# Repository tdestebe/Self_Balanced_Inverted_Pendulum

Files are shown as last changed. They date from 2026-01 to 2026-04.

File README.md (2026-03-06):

# Self_Balanced_Inverted_Pendulum

Self Balanced Inverted Pendulum

This project aims to build an inverted pendulum stabilized by a single reaction wheel. The position of the pendulum is detected by a 3-axis analog gyroscope sensor (MPU6050 module). The position is analyzed inside an Arduino Nano that sends appropriate signals to a motor (Nidec 24H404H160). 

## 3D CAD Model

The assembly of the CAD models and parts are designed with FreeCAD. Following worbenchs are used:

- **Part design** to design 3D mechanical parts

- **Assembly 4.1** based on local axis systems

- **Fasteners** for all screws and nuts

- **Mesh** to create and export STL files

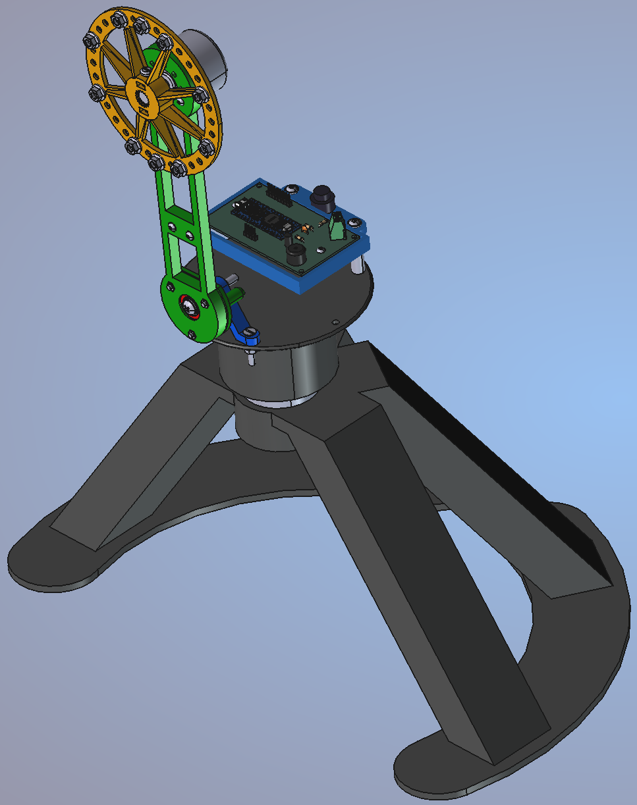
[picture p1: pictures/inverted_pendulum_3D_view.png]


**Inverted pendulum - FreeCAD mesh export**

FreeCAD files are available at [freeCad](https://github.com/tdestebe/Self_Balanced_Inverted_Pendulum/tree/main/freeCad)

STL 3D files are at [STL_files](https://github.com/tdestebe/Self_Balanced_Inverted_Pendulum/tree/main/STL_files)

## Simulation with openModelica

Simulation is performed through an openModelica implementation into the package SelfBalancedWheelPackage. Main Modelica model **SingleWheelRobot** calls model **Dynamics** in which PID, Motor, etc are implemented and calls model **Animation** to display rotation of 3D models of the reaction wheel and the arm. 

thumbnail

**Inverted pendulum - Modelica main model**

<table border="0" style="width: 100%;">
  <!-- Current Row -->
  <tr>
    <th style="border: none; text-align: center; font-weight: bold;">thumbnail</th>
    <th style="border: none; text-align: center; font-weight: bold;"></th>
    <th style="border: none; text-align: center; font-weight: bold;">thumbnail</th>
  </tr>
  <!-- Header Rows -->
  <tr>
    <td style="border: none;"><b>Inverted pendulum - Modelica Dynamics model</b></td>
    <td style="border: none; text-align: center; font-weight: bold;"></td>
    <td style="border: none;"><b>Inverted pendulum - Modelica Animation model</b></td>
  </tr>
</table>

Source files are available at [Self Balaced Wheel Package](https://github.com/tdestebe/Self_Balanced_Inverted_Pendulum/tree/main/SelfBalancedWheelPackage)

## Arduino code and circuits

### Code (.ino)

The source code for Arduino is provided at [code](https://github.com/tdestebe/Self_Balanced_Inverted_Pendulum/tree/main/code). It is similar to the code written by **Remigijus** (see [remrc - One-Axis-Reaction-Wheel-Stick](https://github.com/remrc/One-Axis-Reaction-Wheel-Stick)).

### Fritzing schema

The schema is also identical to the original one posted by Remigijus. I just rewrote it with Fritzing, including a breadboard and stored the source at [circuit](https://github.com/tdestebe/Self_Balanced_Inverted_Pendulum/tree/main/circuit).

<table border="0" style="width: 100%;">
  <!-- Current Row -->
  <tr>
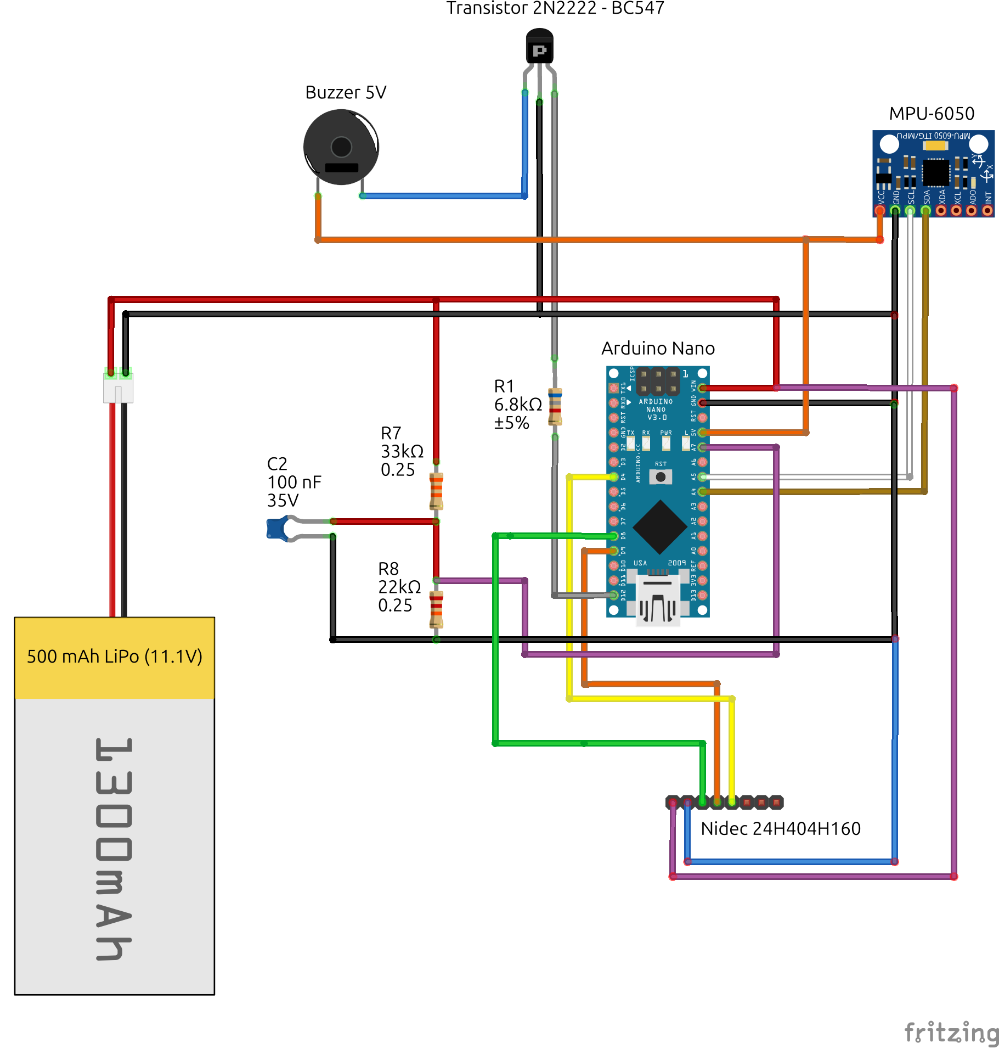
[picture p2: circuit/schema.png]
    <th style="border: none; text-align: center; font-weight: bold;"></th>
    <th style="border: none; text-align: center; font-weight: bold;"></th>
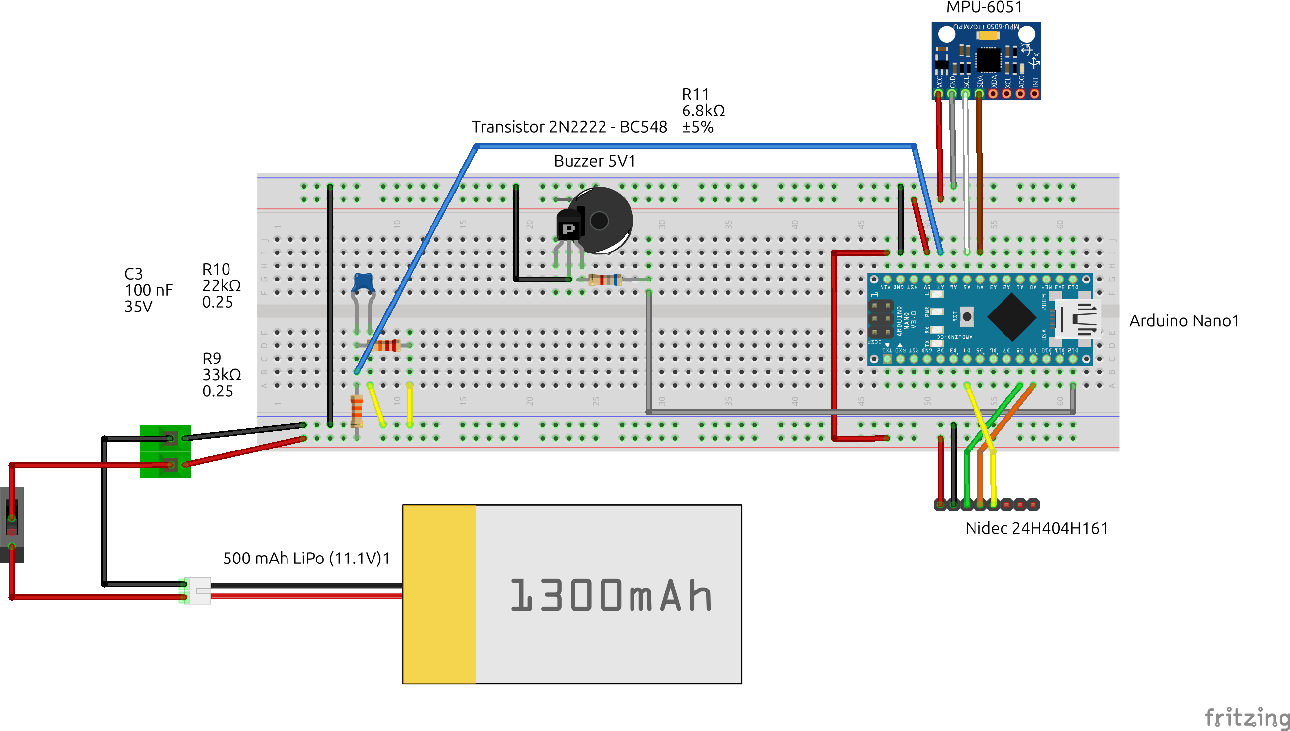
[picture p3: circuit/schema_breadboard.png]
    <th style="border: none; text-align: center; font-weight: bold;"></th>
  </tr>
  <!-- Header Rows -->
  <tr>
    <td style="border: none;"><b>Fritzing schema - Original</b></td>
    <td style="border: none; text-align: center; font-weight: bold;"></td>
    <td style="border: none;"><b>Fritzing schema - Breadboard</b></td>
  </tr>
</table>

### KiCad circuit

In addition to Fritzing schema, I implemented KiCad schematic circuit and generated a KiCad PCB for visualisation into the 3D CAD assembly. 

Kicad project is stored at [kiCAD](https://github.com/tdestebe/Self_Balanced_Inverted_Pendulum/tree/main/kiCAD).

<table border="0" style="width: 100%;">
  <!-- Current Row -->
  <tr>
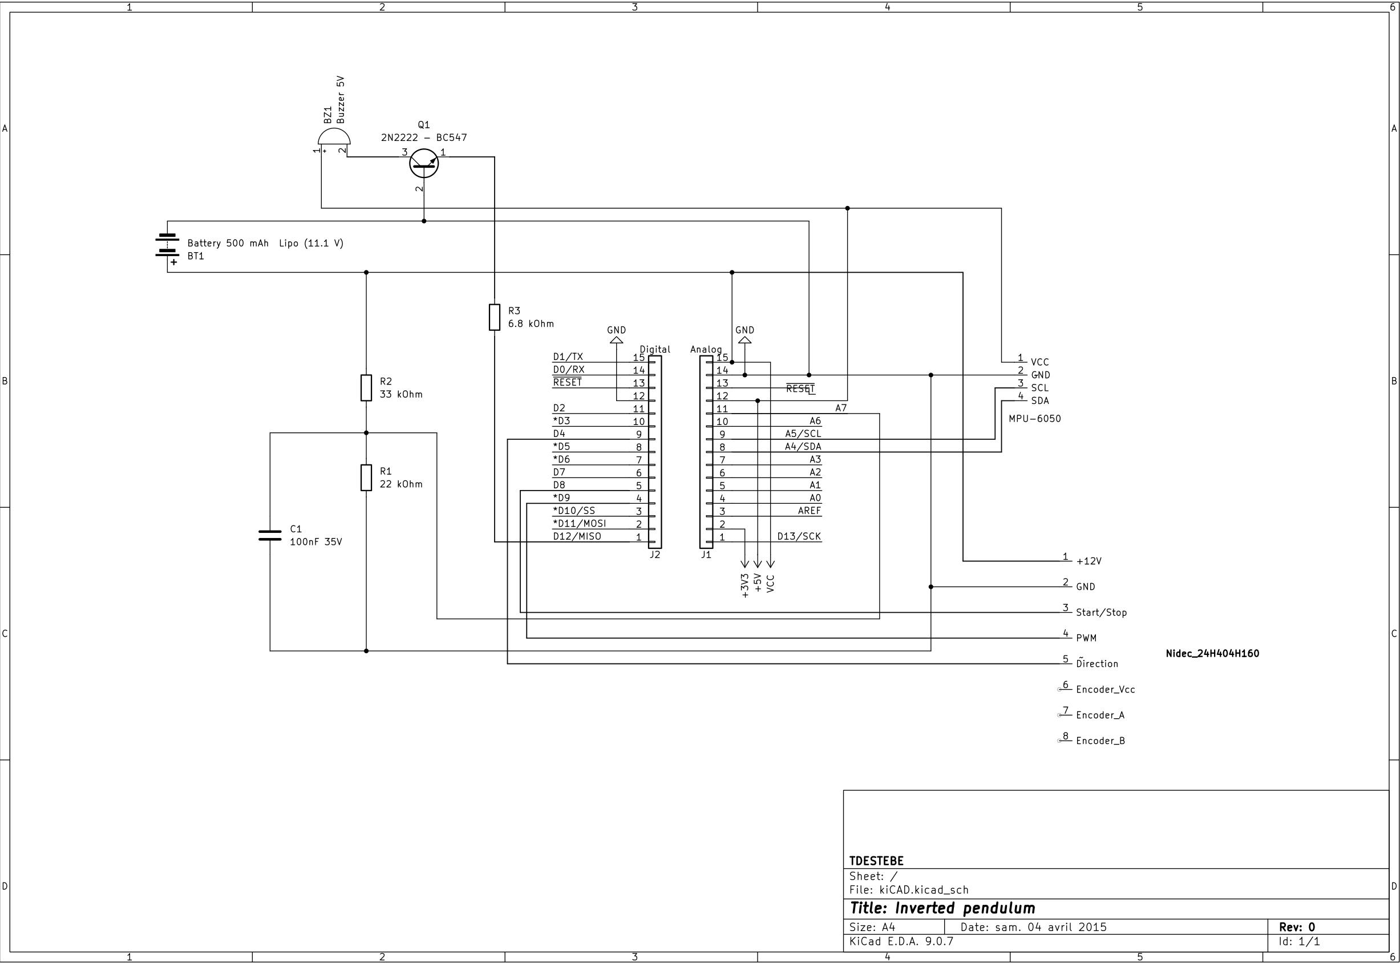
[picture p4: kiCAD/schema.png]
    <th style="border: none; text-align: center; font-weight: bold;"></th>
    <th style="border: none; text-align: center; font-weight: bold;"></th>
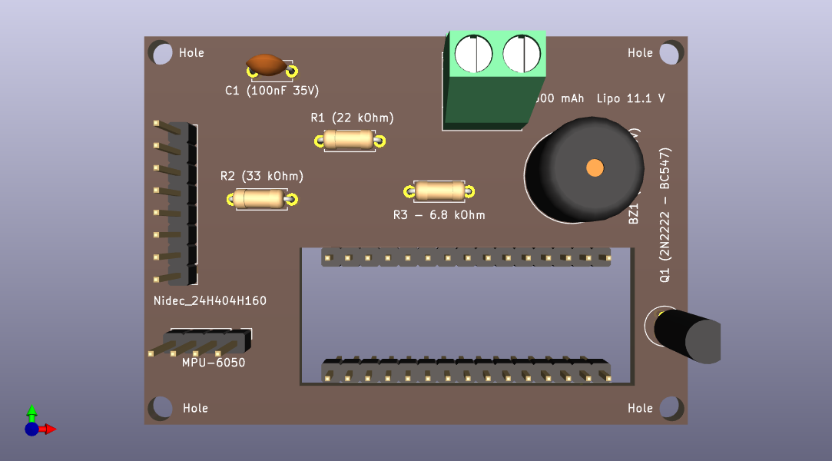
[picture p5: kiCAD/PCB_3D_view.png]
    <th style="border: none; text-align: center; font-weight: bold;"></th>
  </tr>
  <!-- Header Rows -->
  <tr>
    <td style="border: none;"><b>KiCad circuit - Schema</b></td>
    <td style="border: none; text-align: center; font-weight: bold;"></td>
    <td style="border: none;"><b>KiCad circuit - PCD 3D view</b></td>
  </tr>
</table>

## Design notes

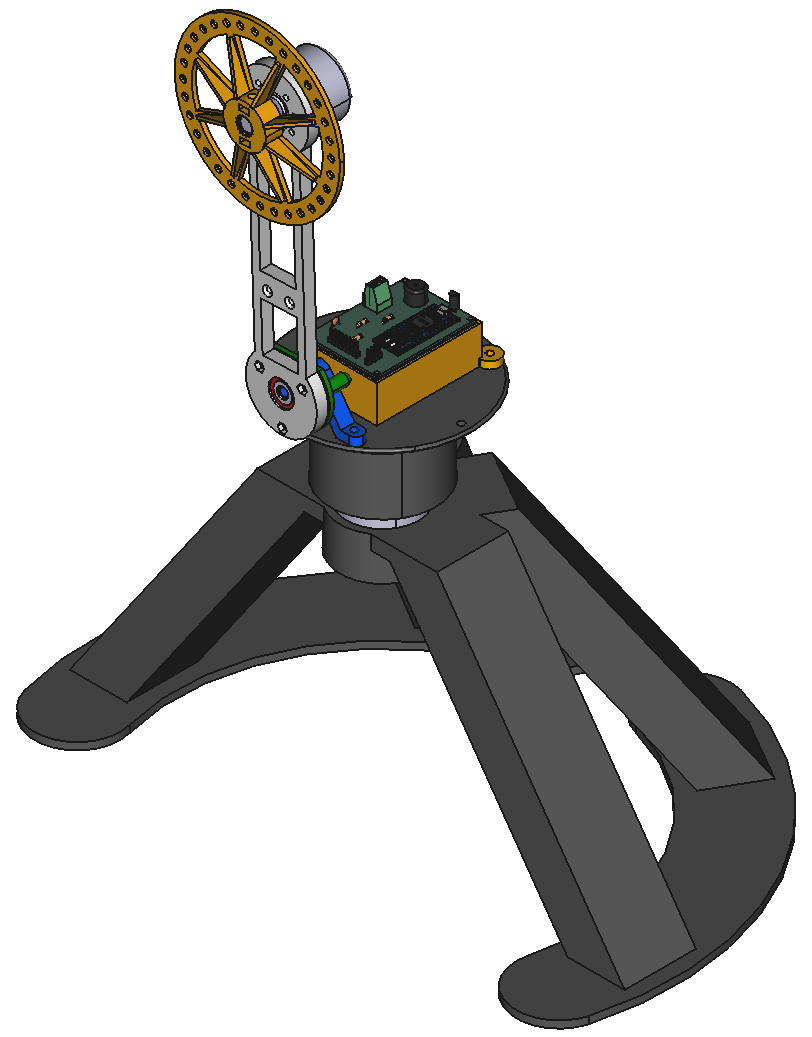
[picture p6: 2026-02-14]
SelfBalancedWheelPackage/robot.png

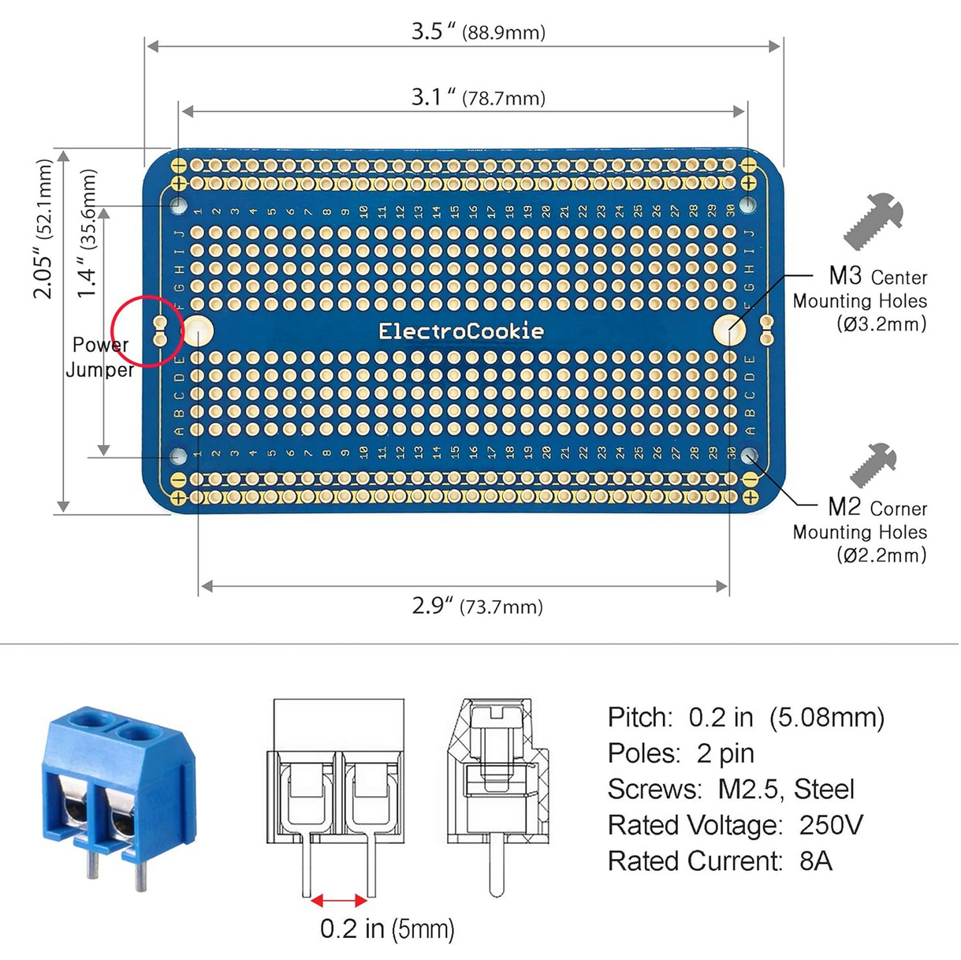
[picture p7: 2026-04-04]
freeCad/ProtoBoard/PCB_prototypage.png

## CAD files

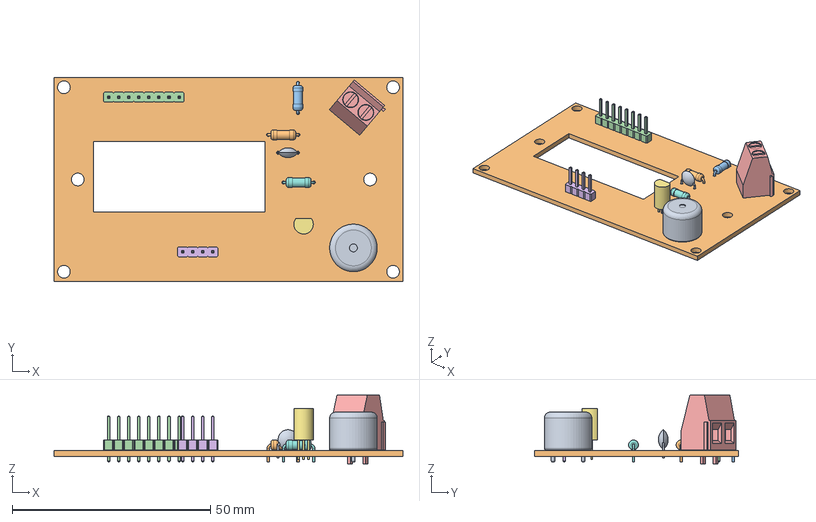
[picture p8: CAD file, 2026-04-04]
freeCad/main_circuit_board.FCStd
88.0 x 51.5 x 17.3 mm
C_Disc_D5.0mm_W2.5mm_P5.00mm
R_Axial_DIN0207_L6.3mm_D2.5mm_P7.62mm_Horizontal
R_Axial_DIN0207_L6.3mm_D2.5mm_P7.62mm_Horizontal001
PinHeader_1x08_P2.54mm_Vertical
TerminalBlock_Phoenix_MKDS-1,5-2_1x02_P5.00mm_Horizontal
PinHeader_1x04_P2.54mm_Vertical
TO-92L_Inline
R_Axial_DIN0207_L6.3mm_D2.5mm_P7.62mm_Horizontal002
Buzzer_12x9.5RM7.6
kiCAD_PCB

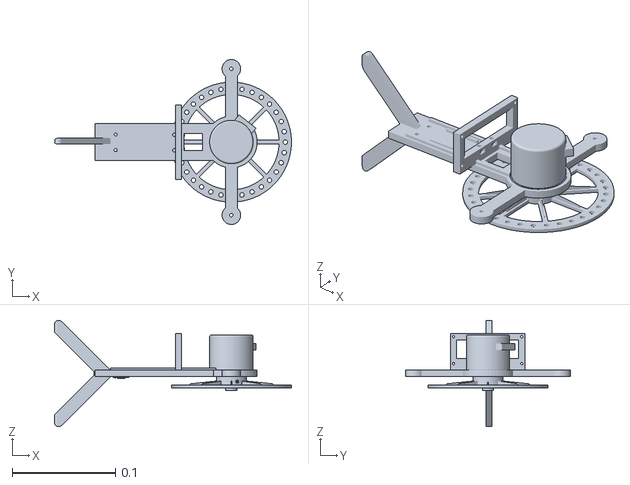
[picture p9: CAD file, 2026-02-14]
SelfBalancedWheelPackage/Resources/assembly_all_meshed.stl
0.229 x 0.159 x 0.103

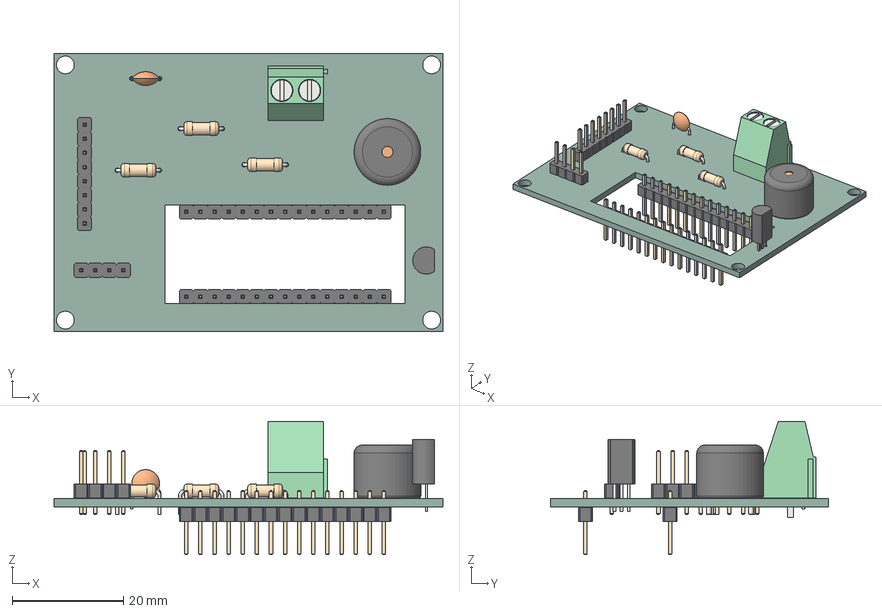
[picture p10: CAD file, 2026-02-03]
freeCad/main_Circuit-kicad_Circuit.STEP
70.0 x 50.0 x 24.0 mm
C_Disc_D5.0mm_W2.5mm_P5.00mm
R_Axial_DIN0207_L6.3mm_D2.5mm_P7.62mm_Horizontal x 3
PinHeader_1x08_P2.54mm_Vertical
TerminalBlock_Phoenix_MKDS-1,5-2_1x02_P5.00mm_Horizontal
PinHeader_1x04_P2.54mm_Vertical
TO-92L_Inline
Buzzer_12x9.5RM7.6
PinHeader_1x15_P2.54mm_Vertical x 2
kicadTest_PCB

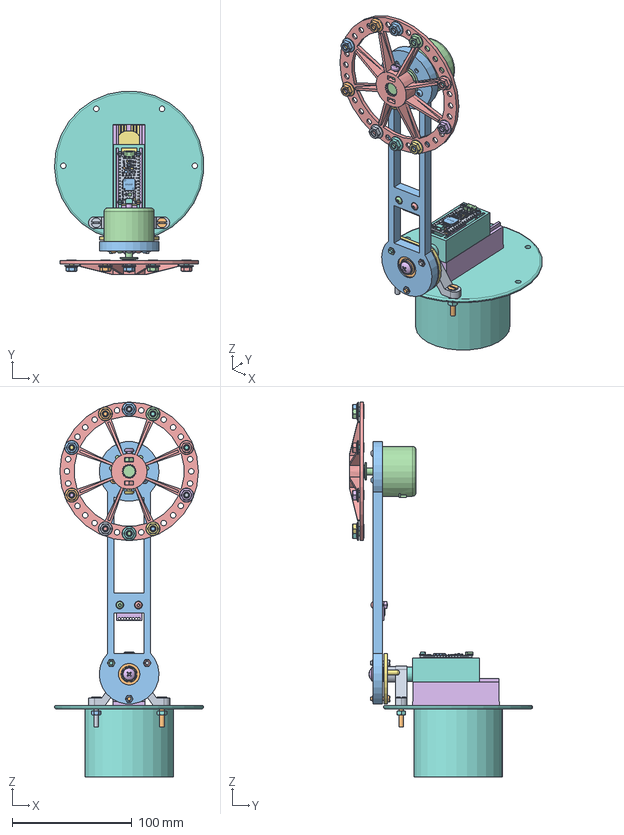
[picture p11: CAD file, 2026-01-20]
freeCad/assembly_Pendulum.FCStd
124.7 x 153.5 x 313.7 mm
Body_Support
Body_Bearing
Body_Arm
Body_Motor
Body_ReactionWheel
Body_MPU6050
Body_BearingLock
Body_Box_Arduino
CAP-0402
FER-0603
CAP-0603
Extruded
SOT-23
lead
lead001
RES-0402
Leader
Leader001
Leader002
Extruded001
Extruded002
RES-0403
RES-0404
RES-0405
Extruded003
Extruded004
Extruded005
Extruded006
CAP-0604
sot25
CAP-0605
RES-0406
RES-0407
RES-0408
RES-0409
SOT-024
SM04B-SRSS-TB_RGB12040119
quartz_3_2__2_5_16MHz v2
RES-0410
RES-0411
RES-0412
RES-0413
FER-0604
CAP-0606
CAP-0607
CAP-0608
CAP-0609
CAP-0610
CAP-0611
CAP-0612
CAP-0613
CAP-0614
Leader003
Leader004
Leader005
Leader006
Leader007
Leader008
Leader009
Leader010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

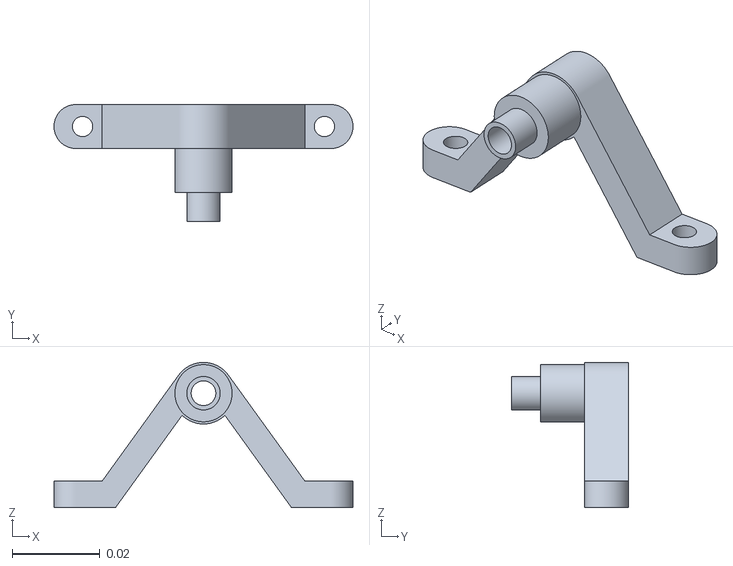
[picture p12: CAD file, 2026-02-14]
SelfBalancedWheelPackage/Resources/Shapes/scale_Simu-04_Support.stl
0.068 x 0.0266 x 0.033

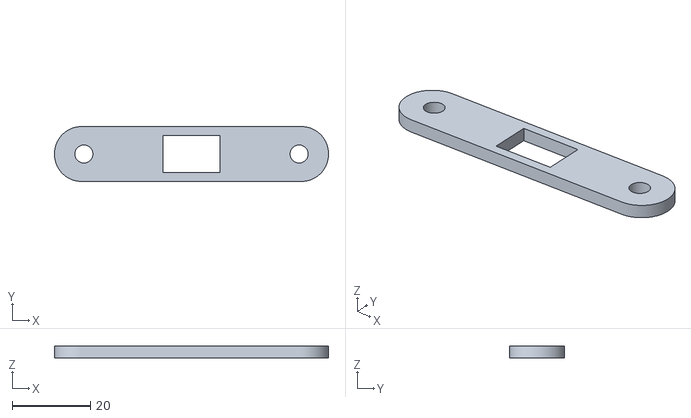
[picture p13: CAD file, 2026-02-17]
STL_files/Body_button_handle (Meshed).stl
70.0 x 14.0 x 3.00

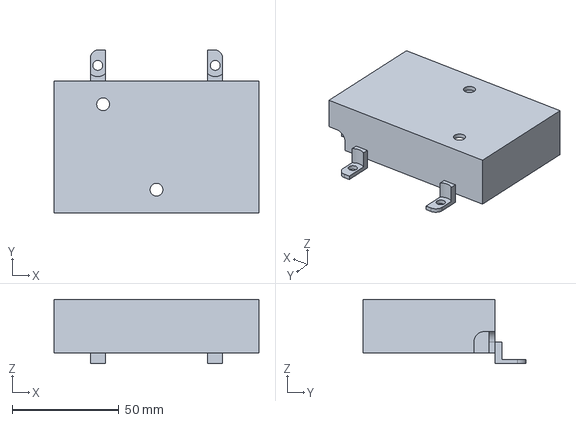
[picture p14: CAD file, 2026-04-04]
freeCad/circuit_housing.FCStd
96.0 x 76.5 x 30.0 mm

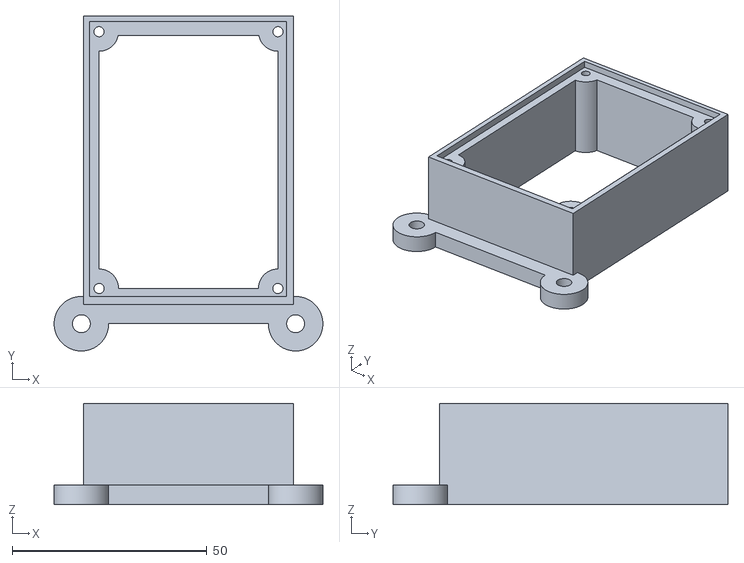
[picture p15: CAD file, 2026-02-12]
STL_files/Body_circuit_house (Meshed).stl
69.0 x 86.0 x 26.0

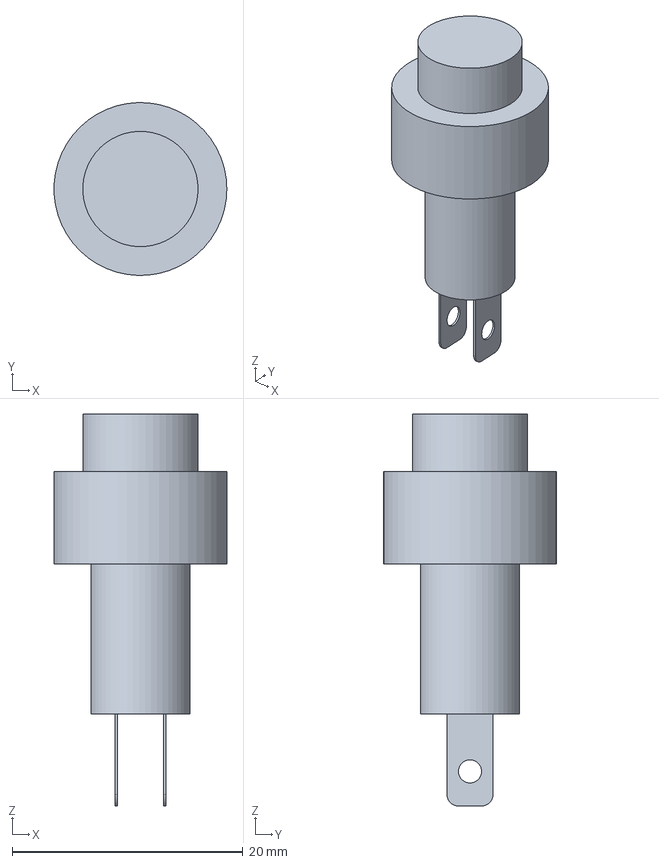
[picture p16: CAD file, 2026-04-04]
freeCad/button_round.FCStd
15.0 x 15.0 x 34.0 mm

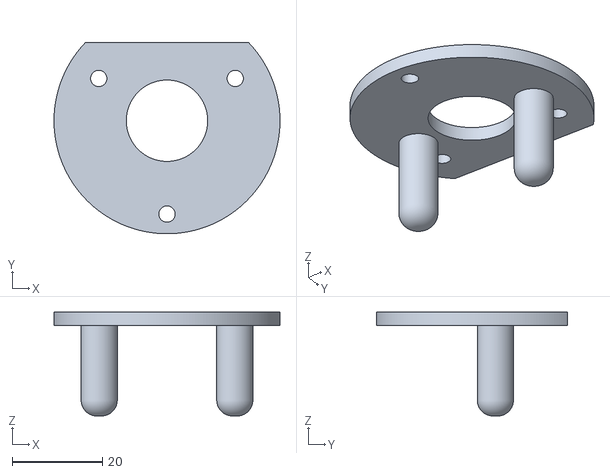
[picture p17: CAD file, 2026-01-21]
STL_files/Body_BearingLock (Meshed).stl
50.0 x 42.3 x 23.0

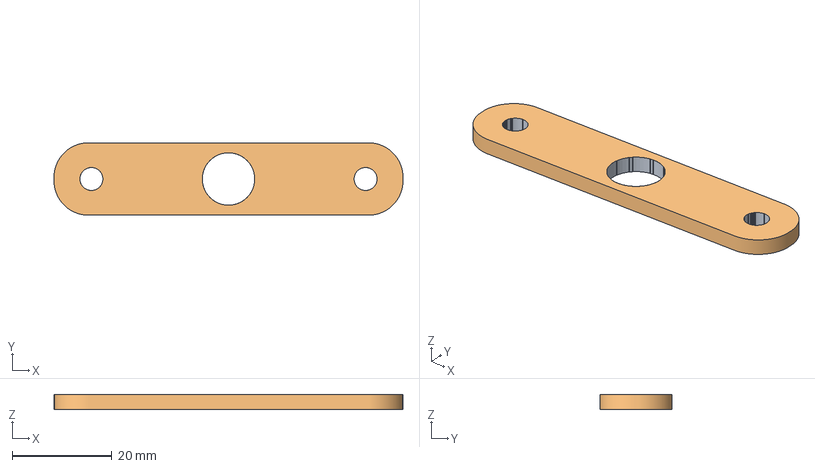
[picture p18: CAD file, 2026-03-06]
freeCad/button.FCStd
70.0 x 14.5 x 3.00 mm
Body_button_handle_Hole
Body_button_handle_Hole (Meshed)

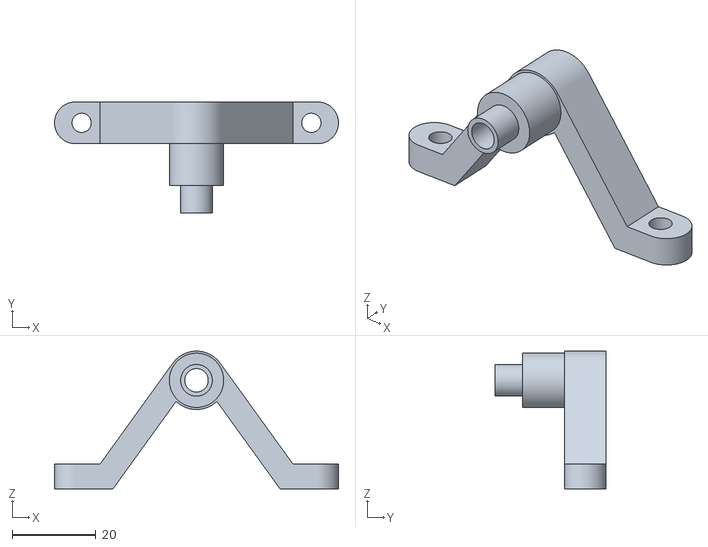
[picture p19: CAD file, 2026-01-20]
STL_files/Body_Support (Meshed).stl
68.0 x 26.6 x 33.0

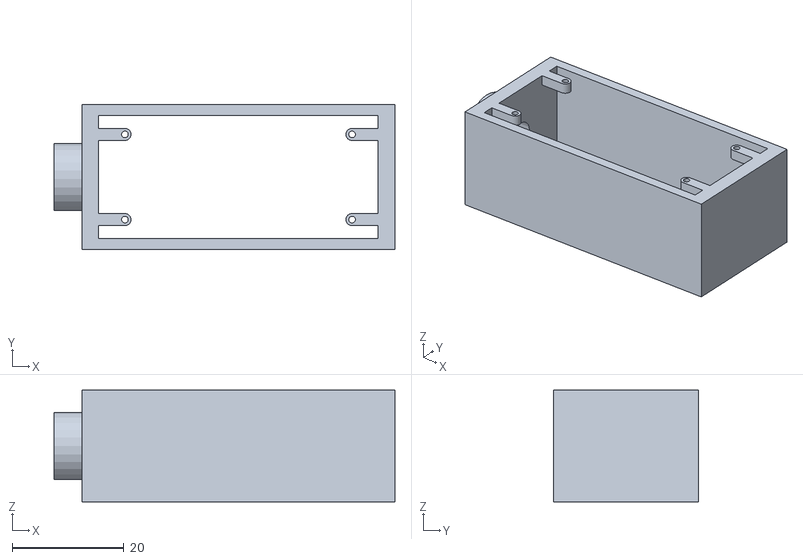
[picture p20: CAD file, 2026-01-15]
STL_files/Body_Box_Arduino (Meshed).stl
61.0 x 26.0 x 20.0

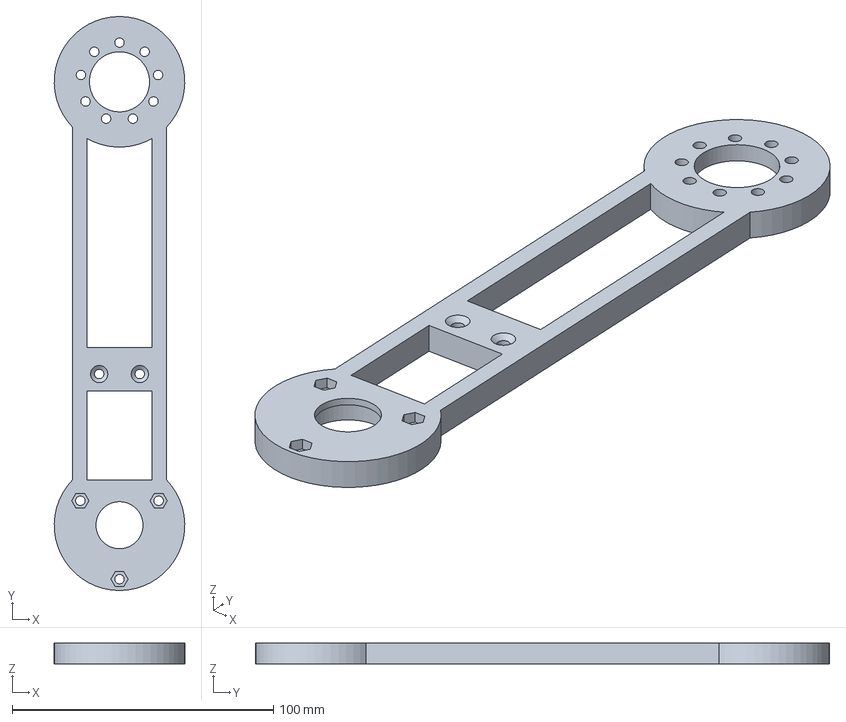
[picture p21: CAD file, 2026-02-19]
freeCad/pendulum_Arm.FCStd
50.0 x 219.7 x 8.00 mm

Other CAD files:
kiCAD/.step
kiCAD/kiCad_Board.step
freeCad/pendulum_BearingLock.FCStd
STL_files/Body_Front_Left (Meshed).stl
STL_files/Body_Arm (Meshed).stl
STL_files/Body_Circuit_House (Meshed).stl
STL_files/Body_Front_Right (Meshed).stl
STL_files/Body_ReactionWheel (Meshed).stl
STL_files/Body_Rondelle (Meshed).stl
freeCad/Ball_Bearing_22mm_OD-8mm_ID.FCStd
freeCad/MPU6050.FCStd
freeCad/arduino_Nano-Rev3_0.fcstd
freeCad/arduino_Nano_PCB.fcstd
freeCad/battery_Tattu_450.FCStd
freeCad/pendulum_Motor_Nidec_24H.FCStd
freeCad/pendulum_Pedestral.FCStd
freeCad/pendulum_Pedestral_connector.FCStd
freeCad/pendulum_Reaction_Wheel.FCStd
freeCad/pendulum_battery_holder.FCStd
freeCad/pendulum_support.FCStd
freeCad/support_Arduino_Pendule.FCStd
freeCad/support_Inverted_Pendulum.FCStd

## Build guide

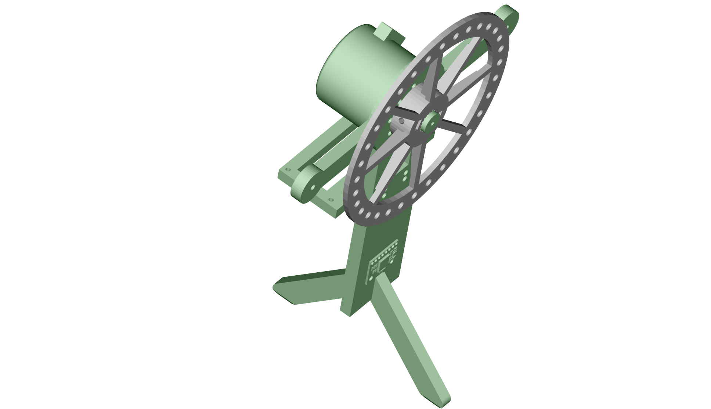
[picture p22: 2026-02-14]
SelfBalancedWheelPackage/Resources/assembly_animation_shape.png

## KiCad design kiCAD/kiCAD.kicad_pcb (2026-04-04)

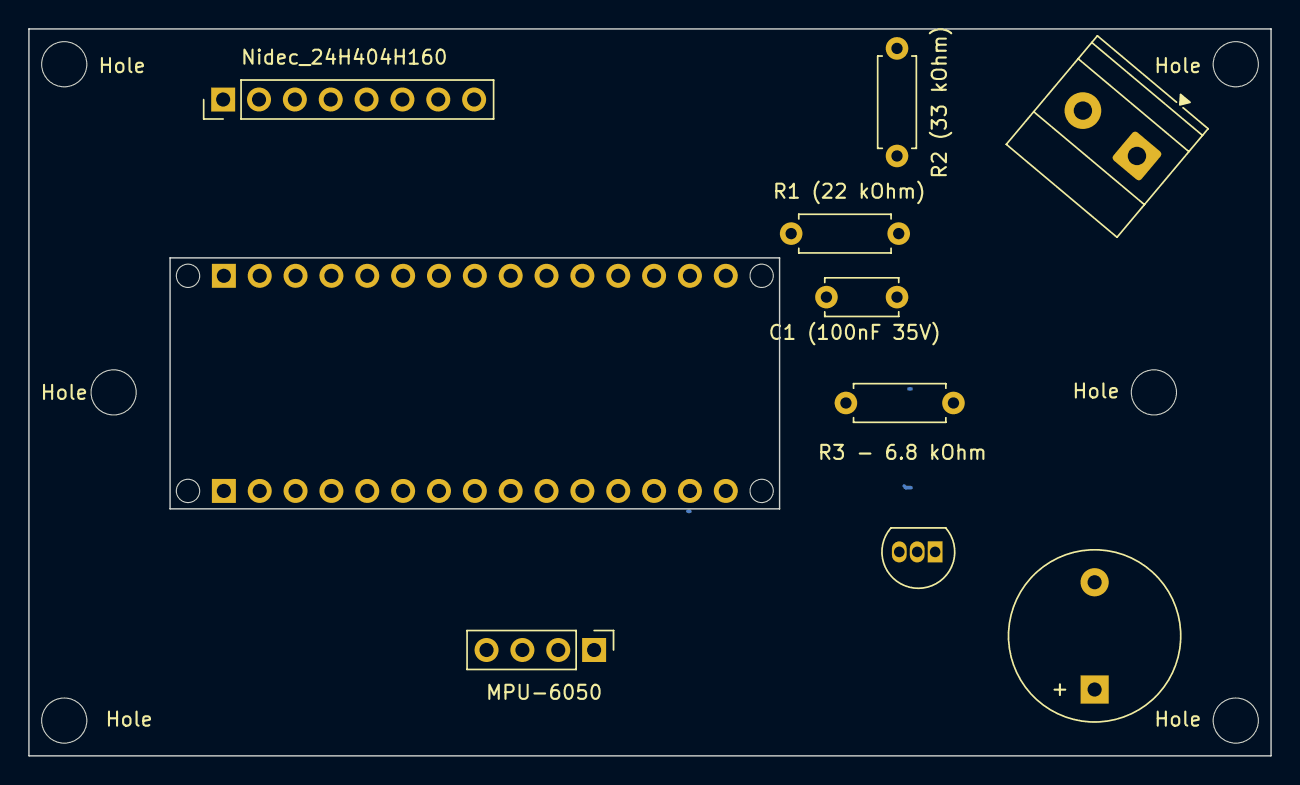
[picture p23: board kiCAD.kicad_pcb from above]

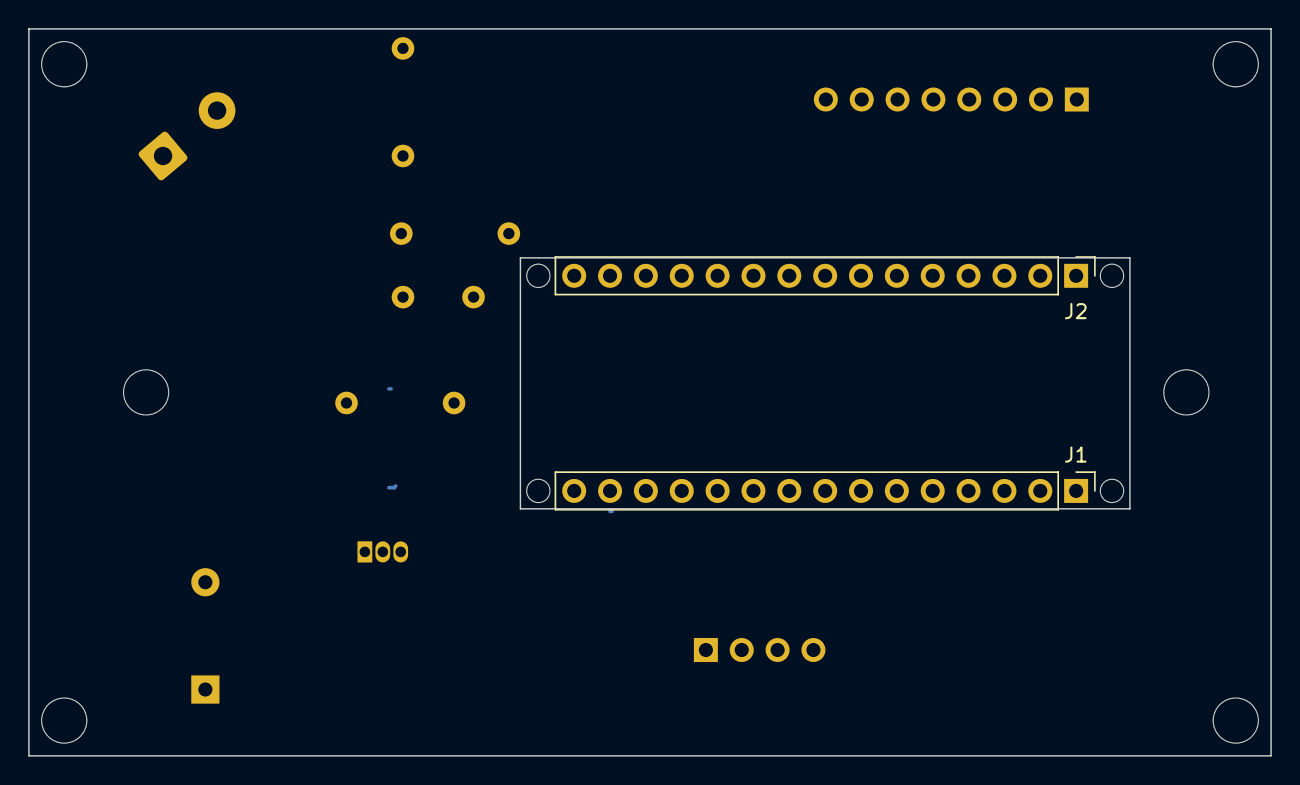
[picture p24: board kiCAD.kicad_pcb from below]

Board: 2 copper layers, 88.0 x 51.5 mm, 21 parts (2 on the bottom side), 13 nets.

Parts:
500 mAh  Lipo 11.1 V: Battery 500 mAh Lipo (11.1 V); TerminalBlock_Phoenix_MKDS-1,5-2_1x02_P5.00mm_Horizontal
BZ1 (Buzzer 5V): Buzzer 5V; Buzzer_12x9.5RM7.6
C1 (100nF 35V): 100nF 35V; C_Disc_D5.0mm_W2.5mm_P5.00mm
Hole: 3.6mm; MountingHole_3.2mm
Hole#2, Hole#3, Hole#4, Hole#6: 2.6mm; MountingHole_3.2mm
Hole#5: 3.6mm; MountingHole_3.2mm
J1: Analog; PinHeader_1x15_P2.54mm_Vertical
J2: Digital; PinHeader_1x15_P2.54mm_Vertical
MH1, MH2, MH3, MH4: MountingHole_65mil
MPU-6050: PinHeader_1x04_P2.54mm_Vertical
Nidec_24H404H160: PinHeader_1x08_P2.54mm_Vertical
Q1 (2N2222 - BC547): 2N2222; TO-92L_Inline
R1 (22 kOhm): 22 kOhm; R_Axial_DIN0207_L6.3mm_D2.5mm_P7.62mm_Horizontal
R2 (33 kOhm): 33 kOhm; R_Axial_DIN0207_L6.3mm_D2.5mm_P7.62mm_Horizontal
R3 - 6.8 kOhm: 6.8 kOhm; R_Axial_DIN0207_L6.3mm_D2.5mm_P7.62mm_Horizontal

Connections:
+5V: BZ1 (Buzzer 5V).1 (+), J1.12, MPU-6050.1 (VCC)
/*D9: J2.4, Nidec_24H404H160.4 (PWM)
/A4/SDA: J1.8, MPU-6050.4 (SDA)
/A5/SCL: J1.9, MPU-6050.3 (SCL)
/A7: C1 (100nF 35V).1, J1.11, R1 (22 kOhm).1, R2 (33 kOhm).2
/D4: J2.9, Nidec_24H404H160.5 (Direction)
/D8: J2.5, Nidec_24H404H160.3 (Start/Stop)
/D12/MISO: J2.1, R3 - 6.8 kOhm.2
/~RESET: J1.13, J2.13
GND: 500 mAh Lipo 11.1 V.2 (-), C1 (100nF 35V).2, J1.14, J2.12, MPU-6050.2 (GND), Nidec_24H404H160.2 (GND), Q1 (2N2222 - BC547).2 (B), R1 (22 kOhm).2
unnamed: BZ1 (Buzzer 5V).2 (-), Q1 (2N2222 - BC547).3 (C)
unnamed: Q1 (2N2222 - BC547).1 (E), R3 - 6.8 kOhm.1
VCC: 500 mAh Lipo 11.1 V.1 (+), J1.15, Nidec_24H404H160.1 (+12V), R2 (33 kOhm).1

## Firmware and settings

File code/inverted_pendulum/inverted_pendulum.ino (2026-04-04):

#include <Wire.h>

#define MPU6050       0x68         // Device address
#define ACCEL_CONFIG  0x1C         // Accelerometer configuration address
#define GYRO_CONFIG   0x1B         // Gyro configuration address
#define PWR_MGMT_1    0x6B
#define PWR_MGMT_2    0x6C

#define BRAKE         8 
#define PWM           9
#define DIRECTION     4

#define BUZZER        12
#define VBAT          A7

const uint16_t PWM_FREQUENCY = 20000;                 // The motor driver can handle a PWM frequency up to 20kHz
const uint16_t PWMVALUE = F_CPU / PWM_FREQUENCY / 2;  // The frequency is given by F_CPU/(2*N*ICR) - where N is the prescaler, prescaling is used so the frequency is given by F_CPU/(2*ICR) - ICR = F_CPU/PWM_FREQUENCY/2

float X1 = 95.0;     // angle gain
float X2 = 14.0;     // gyro damping 
float X3 = 0.08;     // wheel speed damping

//float X1 = 75.0; 
//float X2 = 5.25;   
//float X3 = 0.04; 
 
float loop_time = 10;  // 100 Hz
//float loop_time = 4;   // ChatGPT - 250 Hz - Reaction wheels really benefit from >200 Hz.

int pwm_s = 0;
byte dir;
int32_t motor_speed; 
uint32_t timer;
long currentT, previousT_1, previousT_2 = 0; 
int16_t AcX, AcY, AcZ, GyZ, gyroZ;

//Sensor output scaling
#define accSens 0             // 0 = 2g, 1 = 4g, 2 = 8g, 3 = 16g
#define gyroSens 1            // 0 = 250rad/s, 1 = 500rad/s, 2 1000rad/s, 3 = 2000rad/s
#define Gyro_amount 0.996     // percent of gyro in complementary filter

//IMU offset values
int16_t  AcX_offset = -750;
int16_t  AcY_offset = 360;
int16_t  AcZ_offset = 0;
int16_t  GyZ_offset = 0;
int32_t  GyZ_offset_sum = 0;

float alpha = 0.40; 
float gyroZfilt;

float robot_angle;
float Acc_angle;

bool vertical = false;  

uint8_t i2cData[14]; // Buffer for I2C data

void setup() {
  Serial.begin(115200);

  // Set PWM frequency to 20kHz - see the datasheet http://www.atmel.com/Images/doc8272.pdf page 128-135 
  // Set up PWM, Phase and Frequency Correct on pin 9 (OC1A) & pin 10 (OC1B) with ICR1 as TOP using Timer1
  TCCR1B = (1 << WGM13) | (1 << CS10);  // Set PWM Phase and Frequency Correct with ICR1 as TOP and no prescaling
  ICR1 = PWMVALUE;                      // ICR1 is the TOP value - this is set so the frequency is equal to 20kHz

  // Clear OC1A/OC1B on compare match when up-counting - Set OC1A/OC1B on compare match when downcounting
  TCCR1A = (1 << COM1A1) | (1 << COM1B1);
  setPWM(400); 
  
  Serial.print("PWM: "); Serial.println(PWMVALUE); Serial.print("CPU_FREQ: "); Serial.println(F_CPU); 
  
  pinMode(PWM, OUTPUT);
  pinMode(BUZZER, OUTPUT);
  digitalWrite(BUZZER, LOW);
  pinMode(BRAKE, OUTPUT);
  pinMode(DIRECTION, OUTPUT);
  digitalWrite(BRAKE, HIGH);
  delay(1000);
  angle_setup();
  Serial.println("Angle setup done!");
}

void loop() {
  currentT = millis();
  
  if (currentT - previousT_1 >= loop_time) {
    Tuning(); 
    angle_calc();
    
    if (vertical) {
      digitalWrite(BRAKE, HIGH);
      gyroZ = GyZ / 131.0; // Convert to deg/s
      // gyroZ = GyZ / 65.5; // ChatGPT - Convert to deg/s - correct value for 500 dps mode.
      
      gyroZfilt = alpha * gyroZ + (1 - alpha) * gyroZfilt;
      pwm_s = -constrain(X1 * robot_angle + X2 * gyroZfilt + X3 * -motor_speed, -255, 255); 
      Serial.print("Motor speed: "); Serial.println(pwm_s);
      Motor_control(pwm_s);
      motor_speed += pwm_s;
      // motor_speed = motor_speed * 0.995 + pwm_s; // ChatGPT - This prevents fake runaway integration.
    } else {
      Motor_control(0);
      digitalWrite(BRAKE, LOW);
      motor_speed = 0;
    }
    previousT_1 = currentT;
  }
  if (currentT - previousT_2 >= 500) {
    battVoltage((double)analogRead(VBAT) / 53.7);  // This is then connected to a 47k-12k voltage divider
    previousT_2 = currentT;
  }
}

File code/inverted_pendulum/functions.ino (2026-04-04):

void writeTo(byte device, byte address, byte value) {
  Wire.beginTransmission(device);
  Wire.write(address);
  Wire.write(value);
  Wire.endTransmission(true);
}

void angle_setup() {
  Wire.begin();
  delay (100);
  Serial.println("Angle setup");
  writeTo(MPU6050, PWR_MGMT_1, 0);
  writeTo(MPU6050, ACCEL_CONFIG, accSens << 3); // Specifying output scaling of accelerometer
  writeTo(MPU6050, GYRO_CONFIG, gyroSens << 3); // Specifying output scaling of gyroscope
  delay (100);
  Serial.println("MPU6050 is awake!");
  for (int i = 0; i < 1024; i++) {
    angle_calc();
    GyZ_offset_sum += GyZ;
    delay (5);
  }
  GyZ_offset = GyZ_offset_sum >> 10;
  digitalWrite(BUZZER, HIGH);
  delay(70);
  digitalWrite(BUZZER, LOW);
  delay(80);
  digitalWrite(BUZZER, HIGH);
  delay(70);
  digitalWrite(BUZZER, LOW);
  Serial.print("GyZ offset value = "); Serial.println(GyZ_offset);
}

void angle_calc() {
  
  Wire.beginTransmission(MPU6050);
  Wire.write(0x3B);                  
  Wire.endTransmission(false);
  Wire.requestFrom(MPU6050, 4, true);
  AcX = Wire.read() << 8 | Wire.read(); // 0x3B (ACCEL_XOUT_H) & 0x3C (ACCEL_XOUT_L)
  AcY = Wire.read() << 8 | Wire.read(); // 0x3D (ACCEL_YOUT_H) & 0x3E (ACCEL_YOUT_L)

//  Wire.requestFrom(MPU6050, 6, true); // ChatGPT
//  AcX = Wire.read() << 8 | Wire.read();
//  AcY = Wire.read() << 8 | Wire.read();
//  AcZ = Wire.read() << 8 | Wire.read();

  Wire.beginTransmission(MPU6050);
  Wire.write(0x47);
  Wire.endTransmission(false);
  Wire.requestFrom(MPU6050, 2, true);  
  GyZ = Wire.read() << 8 | Wire.read(); 

  AcX += AcX_offset;
  AcY += AcY_offset;  
  AcZ += AcZ_offset;
  GyZ -= GyZ_offset;

  robot_angle += GyZ * loop_time / 1000 / 65.536; 
  Acc_angle = atan2(AcY, -AcX) * 57.2958;               // angle from acc. values       * 57.2958 (deg/rad)
  robot_angle = robot_angle * Gyro_amount + Acc_angle * (1.0 - Gyro_amount);
  
  if (abs(robot_angle) > 9) vertical = false;
  if (abs(robot_angle) < 0.3) vertical = true;

//  Serial.print(" Acc_angle: "); Serial.print(Acc_angle);
//  Serial.print(" Angle: "); Serial.println(robot_angle);
}

void battVoltage(double voltage) {
  // Serial.print("batt: "); Serial.println(voltage); //debug
  if (voltage > 8 && voltage <= 9.5) {
    digitalWrite(BUZZER, HIGH);
  } else {
    digitalWrite(BUZZER, LOW);
  }
}

void setPWM(uint16_t dutyCycle) { // dutyCycle is a value between 0-ICR1
    OCR1A = dutyCycle;
}

void Motor_control(int pwm) {
  if (pwm <= 0) {
    digitalWrite(DIRECTION, LOW);
    pwm = -pwm;
  } else {
    digitalWrite(DIRECTION, HIGH);
  }
  setPWM(map(pwm, 0, 255, PWMVALUE, 0));
}

int Tuning() {
  if (!Serial.available())  return 0;
  delay(2);
  char param = Serial.read();               // get parameter byte
  if (!Serial.available()) return 0;
  char cmd = Serial.read();                 // get command byte
  Serial.flush();
  switch (param) {
    case 'p':
      if (cmd == '+')    X1 += 1;
      if (cmd == '-')    X1 -= 1;
      printValues();
      break;
    case 'i':
      if (cmd == '+')    X2 += 0.01;
      if (cmd == '-')    X2 -= 0.01;
      printValues();
      break;
     case 's':
      if (cmd == '+')    X3 += 0.005;
      if (cmd == '-')    X3 -= 0.005;
      printValues();
      break;  
  }
}

void printValues() {
  Serial.print("X1: "); Serial.print(X1);
  Serial.print(" X2: "); Serial.print(X2);
  Serial.print(" X3: "); Serial.println(X3, 3);
}

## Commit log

2026-01-04 Create pendulum_Arm.FCStd
    Initial CAD arm file.
    [pendulum_Arm.FCStd]
2026-01-04 Added CAD models
    Bearing ball created and pendulum arm updated.
    [Ball_Bearing_22mm_OD-8mm_ID.FCStd, pendulum_Arm.FCStd]
2026-01-04 Create motor_Nidec_24H.FCStd
    Created CAD model of Nidec 24H motor.
    [motor_Nidec_24H.FCStd]
2026-01-06 Created initial assembly
    Added some 3D components and created initial assembly with.
    [Ball_Bearing_22mm_OD-8mm_ID.FCStd, assembly_Pendulum.FCStd, motor_Nidec_24H.FCStd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]
2026-01-07 Added MPU6050 module
    Created and added MPU6050 CAD model into assembly.
    [MPU6050.FCStd, assembly_Pendulum.FCStd]
2026-01-07 Update assembly_Pendulum.FCStd
    Added some screws
    [assembly_Pendulum.FCStd]
2026-01-08 Added screws and exported Arm
    Added screws into the assembly and exported CAD model of Arm in STL file
    [Body_Arm (Meshed).stl, assembly_Pendulum.FCStd]
2026-01-08 Updated assembly and exported 3D view
    Screws are up-to-date and I exported a 3D view.
    [assembly_Pendulum.FCStd]
2026-01-10 Modified design
    Arm design modified for a better link with bearing.
    [Body_Arm (Meshed).stl, Body_BearingLock (Meshed).stl, Body_ReactionWheel (Meshed).stl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]
2026-01-12 adapted dimensions
    Modified 3D model with more convenient dimensions.
    [Body_Arm (Meshed).stl, Body_Support (Meshed).stl, assembly_Pendulum.FCStd]
2026-01-12 Next step
    Prepare next files
    [Body_Front_Left (Meshed).stl, Body_Front_Right (Meshed).stl, arduino_Nano-Rev3_0.fcstd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]
2026-01-13 Added Arduino stuff
    Added Arduino Nano CAD model and box.
    [arduino_Nano-Rev3_0.fcstd, arduino_Nano_PCB.fcstd, assembly_Pendulum.FCStd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]
2026-01-15 re-organize folder
    Export modified CAD models from the assembly. Delete old obsolete ones.
    [Body_Box_Arduino (Meshed).stl, assembly_Pendulum.FCStd, motor_Nidec_24H.FCStd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]
2026-01-15 Created battery holder
    Created CAD model of battery holder and assembled it with battery
    [assembly_Pendulum.FCStd, battery_Tattu_450.FCStd, main_Box.FCStd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]
2026-01-20 Added foot for pendulum
    Added a foot to fix pendulum
    [Body_Support (Meshed).stl, assembly_Pendulum.FCStd, support_Inverted_Pendulum.FCStd]
2026-01-20 Minor change
    Minor change before next step
    [assembly_Pendulum.FCStd]
2026-01-21 Added pedestral 3D CAD model
    Added a full pedestal to support inverted pendulum.
    [Body_BearingLock (Meshed).stl, pendulum_Pedestral.FCStd, pendulum_Pedestral_connector.FCStd]
2026-01-22 Added animation
    Created a variable to animate the assembly. Arm can balance from -12° to 12°.
2026-01-22 Added circuit
    Added Fritzing file with Arduino based circuit and its exported view.
    [schema.fzz]
2026-01-23 Tested scew in Assembly
    Screw group can move to Assembly for animations.
2026-01-24 added main arduino code
    Same as in https://github.com/remrc/One-Axis-Reaction-Wheel-Stick
2026-01-31 Added Circuit
    Added electronic parts to CAD models
2026-01-31 Updated assembly
    Updated assembly with circuit and box.
    [Body_Circuit_House (Meshed).stl, circuit_housing.FCStd]
2026-02-02 Updated assembly
    Modified circuit box with a hole for axial screw.
    [Body_circuit_house (Meshed).stl]
2026-02-03 Added KiCad project
    Added kiCad files with schematics and 3D view of Arduino circuits. PCB design not complete.
    [kiCAD.kicad_pcb, kiCAD.kicad_sch, main_Box.FCStd]
2026-02-04 Minor update
    Updated transitor name with BC547
    [kiCAD.kicad_pcb, kiCAD.kicad_sch, schema.fzz]
2026-02-12 Completed hardware and run
    Hardware is complete with breadboard. CAD assembly is complete as well.
    Arduino code is almost tuned so that inverted pendulum is self balanced.
    [Body_circuit_house (Meshed).stl, Pendulum.kicad_pcb, Pendulum.kicad_sch]
2026-02-14 Simulation running
    Complete CAD model added to simulation with openModelica.
    [assembly_all_meshed.stl, scale_Simu-04_Support.stl, schema.fzz]
2026-02-17 Updated simulation
    Modified simulation for more realistic rotation of reaction wheel.
    Added CAD model of a button and its holder.
    Minor changes on STL files.
    [Body_button_handle (Meshed).stl, button.FCStd]
2026-02-18 Added schema
    New Fritzing schematics with breadboard.
    [schema_breadboard.fzz]
2026-02-18 Exported picture for README
    Did some clean up and exported view to illustrate circuits.
2026-02-19 FreeCad repository clean up
    Updated freeCad files from Assembly to individual files.
    [pendulum_Arm.FCStd, pendulum_BearingLock.FCStd, pendulum_support.FCStd]
2026-03-06 New button design
    Circular button holder.
    [button.FCStd]
2026-04-04 Updated models
    Updated models to figure out last improvements.
    [.step, button_round.FCStd, circuit_housing.FCStd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]
